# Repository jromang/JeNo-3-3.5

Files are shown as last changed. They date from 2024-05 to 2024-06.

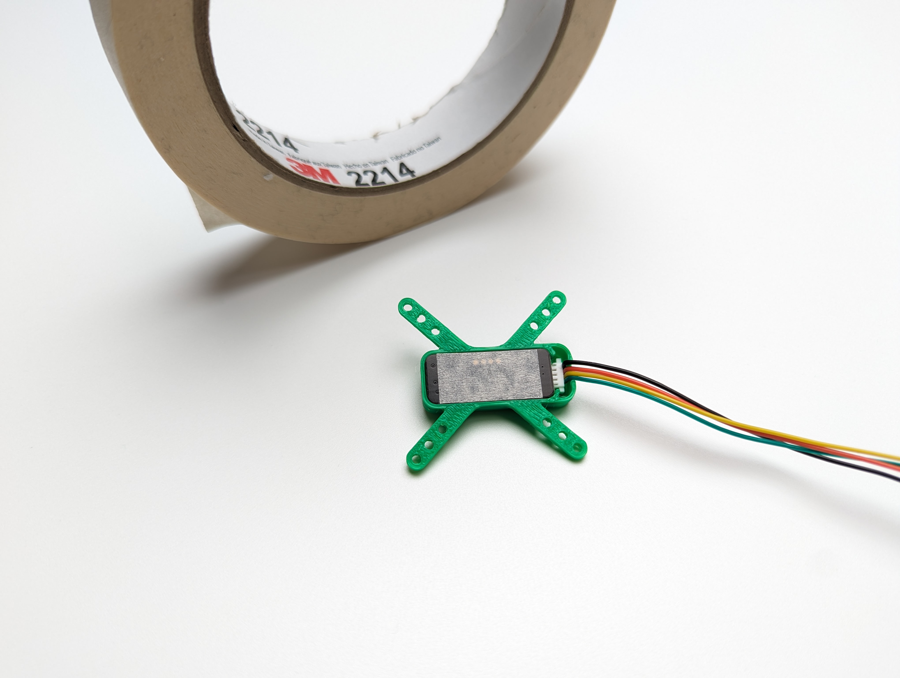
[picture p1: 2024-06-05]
STL/OPTICAL FLOW & LIDAR SENSOR MTF-02 CASE - 6509445/images/1ab90a31-745e-49bc-8f16-971fccf6d18a.jpg

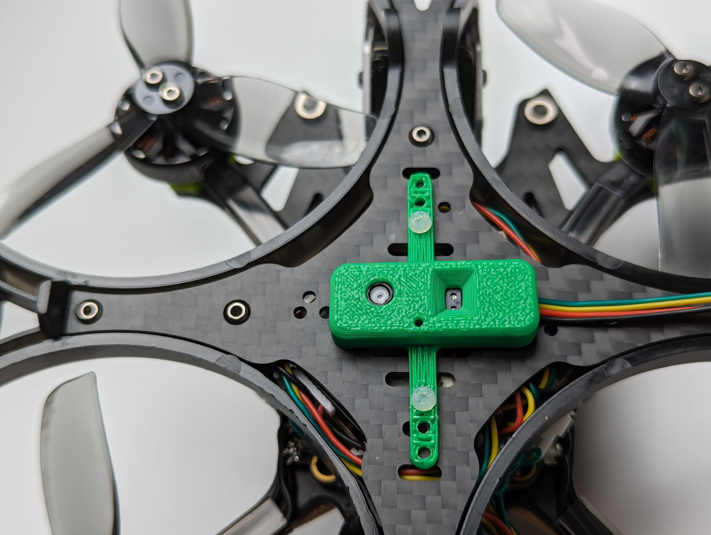
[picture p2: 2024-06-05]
STL/OPTICAL FLOW & LIDAR SENSOR MTF-02 CASE - 6509445/images/625f6806-070a-460f-9479-def415a27e60.jpg

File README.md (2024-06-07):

# Notes de projet JeNo 3

Ce repository contient les notes, liens, et fichiers nécessaires à la construction d'un drone JeNo 3 pouces.

<!-- a normal html comment 

# Liste de courses D

| | Poids unitaire (g) | nombre | Poids total (g) | Prix (€) | Prix unitaire | Remarque |
|-|---|---|---|---|---|---|
|Chassis 3 ‘’ | 56,0 | 1 | 56,0 | 64,50 | 64,50 |
|Stack | 14,4 |1| 14,4 |55,66| 55,66| SpeedyBee F405 Mini 20x20
|Moteur FlyFish | 9,0 |0 |0,0| 62,41
|Moteur Skystars | 8,8| 4 |35,2 |43,84| 43,84 |Skystars Koto 1404 3800KV 3-4S non dispo mais choix ensuite
|Récepteur | 0,7 |1 |0,7 |25,23 |25,23 |FrSky R9 Mini-OTA
|antenne récepteur | 1,5| 1| 1,5
|Gps | 4,3 |1| 4,3| 16,68| 16,68| Walksnail WS-M181
|hélice | 1,50 |4 |6,00| 2,00| 2,00 |HQProp Durable T3x3x3
|Buzzer | 4,00 |1 |4,00 |5,38 |5,38
|Total base | 122,1 |213,29
|Accu 560 mAh | 58,0 |0| 0,0| 19,90| DOGCOM 14,8V 100C 4S
|Accu 450mAh | 53,0 |1| 53,0| 8,63| 8,63| Ovonic 14,8V 80C 4S
|Total base avec accu |175,1 |221,92
|Kit Avatar Moonlight | 38,5 |0 |0,0 |219,90
|camera 4K | 0 |0,0
|antenne FPV | 2,0 |0 |0,0
|total Avatar 4K |0,0
| Kit Avatar HD V2 Dual | 17,6| 1 |17,6 |159,90| 159,90 |en version 32 Go compat Gyroflow
|camera HD V2 | 7,2 |0| 0,0
|antenne HD 2 | 2,0| 2 |4,0
|total Avatar HD V2 | 21,6
|Kit Avatar HD pro dual | 15,4| 0| 0,0 |194,90
|camera HD| 9,5| 0| 0,0
|antenne HD pro| 2,0| 0| 0,0
|total HD pro dual| 0,0
|Total config FPV| 196,7 |381,82

-->

# Liste de courses

| | Poids unitaire (g) | nombre | Poids total (g) | Prix (€) | Prix unitaire | Remarque |
|-|---|---|---|---|---|---|
|Chassis 3 ‘’ | 56,0 | 1 | 56,0 | 53 | 53 | [FVP CNC Drone T700](https://fpvcncdrone.com/product/jeno-3-unibody/)
|Stack | 16.3 |1| 16.3 |69.74| 69.74| [GOKU F722 Pro Mini V2 45A 32Bit 128K 20X20 Stack](https://flywoo.net/products/goku-f722-mini-v2-40a-bls-20x20-stack)
|Moteur  | 8,8| 4 |35,2 |43,84| 43,84 |[ FlyFishRC Flash 1404 4500 KV ](https://www.flyfish-rc.com/products/flash-1404-4500kv-fpv-motor)
|Récepteur | 4 |1 |4 | 15.52 |15.52 | [0.4g Flywoo TCXO 2.4G ELRS EL24E \ EL24P](https://flywoo.net/products/0.4g-flywoo-tcxo-2.4g-elrs-el24e-el24p)
|Gps | 2.2 |1| 2.2 | 17.56| 17.56| [GOKU Nano V3 Flywoo](https://flywoo.net/products/goku-gm10-nano-v3-gps)
|Hélice | 1,50 |4 |6,00| 2,00| 2,00 |HQProp Durable T3x3x3
|Buzzer | 2,7 |1 |2,7 |8.25 |8.25 | [FLYWOO Finder V1.0 w/ LED BUZZER](https://flywoo.net/products/flywoo-finder-v1-0-w-led-buzzer)
|Accu 750mAh | 66,9 |1| 66,9| 15| 15| [Explorer 4S 750mAh HV 80C Lipo Battery - XT30](https://flywoo.net/products/2pcs-explorer-750mah-hv-15-2v-80c-4s1p-lipo-battery-pack-xt30)
|Camera / VTX| 36.4 | 1 | 36.4 | 220 | 249 | [DJI O3 Air Unit](https://www.dji.com/fr/o3-air-unit)
|**Total**|  | | **225,7** | **444.91** |

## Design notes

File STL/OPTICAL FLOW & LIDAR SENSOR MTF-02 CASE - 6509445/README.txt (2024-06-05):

OPTICAL FLOW & LIDAR SENSOR MTF-02 CASE by sr71 on Thingiverse: https://www.thingiverse.com/thing:6509445

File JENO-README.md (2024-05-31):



JeNo 3 - Front view

# JeNo 3" and 3.5"
***3-3.5" drone FPV frame compatible with Air Unit O3 and designed for Freestyle, Freeride and Cinematic. Many customizable options are available.***

> [!NOTE]
> Designed in France by members of the [WE are FPV](https://www.wearefpv.fr/) community, the JeNo is already flown by hundreds of pilots. The French version of the project is available on [Printables](https://www.printables.com/fr/model/459702-jeno-335-drone-frame). Note that a [5.1-6" version](https://github.com/WE-are-FPV/JeNo-5.1) and a [7" version](https://github.com/WE-are-FPV/JeNo-7) of the JeNo exist.

JeNo classic - 3D render

## Table of contents

* [Key features](#key-features)
* [Presentation](#presentation)
* [Detailed specifications](#detailed-specifications)
* [Customization](#customization)
* [Buy it or cut it !](#buy-it-or-cut-it-)
* [Bill of materials](#bill-of-materials)
* [Building/Assembly guide](#buildingassembly-guide)
* [Inspiration](#inspiration)
* [Tuning, Betaflight Preset ?](#tuning-betaflight-preset-)
* [Blackbox](#blackbox)
* [Videos](#videos)
* [Builds examples](#builds-examples)
* [Authors](#authors)
* [TPU](#tpu)
* [Community (remixes and TPU)](#community-remixes-and-tpu)
* [Changelog](#changelog)

## Key features
- [x] **Sturdiness** and **rigidity**
- [x] Excellent flight **performances**, easy to tune
- [x] **Wide-X** geometry
- [x] Perfect DJI **Air Unit O3** camera integration
- [x] Optional soft mounting of the camera for effective Gyroflow stabilization.
- [x] Designed for : DJI Vista/AU O3, WalkSnail, HDZero, Analogic
- [x] **Frame and standoffs NOT visible** in video feed, with any FPV camera
- [x] **Props NOT visible** in video feed !
- [x] Support 20x20 stacks as well as AiO (straight and 45° angled)
- [x] **Customizable** (weight, size, camera plates, unibody or not)

## Presentation
The success of the [JeNo 5.1"](https://github.com/WE-are-FPV/JeNo-5.1) has led us to develop a little brother, in **3 and 3.5"** form factor. This frame will therefore be just **as comfortable for Freestyle as for cinematic** shooting.

On 5" and larger builds, we might be tempted to keep an Action Cam, whereas on a **compact and light machine**, the **DJI O3 reveals its full potential**.

The design of a frame of this size turned out to be more delicate than expected :

* **Weight** is crucial
* **Strength** and **rigidity** remain major concerns
* **Electronics** are more **diversified** : 20x20 stack with separate FC and ESCs, AiO straight or angled at 45°, stack mounting with M2 or M3...
* The low inertia of this format makes the gyro of the O3 camera very sensitive; vibration tolerance is much lower than for a 5" quads
* **Clear FOV** : no spacers, frame, or visible propellers in the FPV feed

After several iterations, we have come to a first version of the JeNo that **ticks all these boxes !** This is the **3" Classic version, unibody with a 4mm bottom plate**.

We were initially not enthusiastic about the unibody design, but this approach has proven to be an **excellent compromise**. With a thickness of 4mm for the bottom plate, we get **exceptional strength** and **flight behavior** worthy of a 5". The assembly remains easy, and the absence of separate arms allows for sliding a 20x20 stack while taking advantage of the 20mm height of the body.

WE are FPV banner

**Other versions** are available :

* 3.5" (unibody) (warning : tips of props slightly visible in the FPV feed)
* 3" (unibody) **Light**
* 3" et 3.5 " with **separate arms**
* 4": this is a variation created by Kennytak, and the necessary files are available on [his page](https://www.printables.com/fr/model/516544-jeno-4-unibody-drone-frame-for-dji03-airunit-vista). The props remain slightly visible in the FPV feed.

The **JeNo 3** follows in the footsteps of its big brother : the front cage tilted at 25° provides a **clear FOV**. Notches are provided to slide in any type of **ND filter**, and the propellers are not visible in the FPV feed or in HD recording.

Two types of camera plates are available : **full carbon** or **soft-mounted**. Note that to benefit from Gyroflow (or RockSteady) stabilization, it is **imperative to opt for the soft-mounted camera plates**.

Finally, as this frame was designed by members of the [WE are FPV](https://www.wearefpv.fr/) **community**, a **"WaF edition"** is available (the logo is engraved on the bottom plate). Join us on the WAF forum in [the official JeNo 3-3.5" thread](https://forum.wearefpv.fr/topic/20437-jeno-335-un-ch%C3%A2ssis-compact-taill%C3%A9-pour-le-dji-o3/) to discuss it further.

WE are FPV banner

The JeNo is also available in [5.1-6" version](https://github.com/WE-are-FPV/JeNo-5.1) and [7" version](https://github.com/WE-are-FPV/JeNo-7).

## Detailed specifications

||| 
| :--- | :--- |
| **Geometry** | **Wide-X** | 
| **Props size** | 3 to 3.5" (depending on the versions) | 
| **Weight** | **40 to 55 g** depending on the versions, including screws | 
| **Arms** | **4mm** for unibody, **3mm** for separate arms | 
| **Body height** | 20 mm | 
| **Stack height** | 20 mm (unibody) | 
| **Bottom plate** | **4mm** for unibody, **2mm** for separate arms | 
| **Middle plate** | 2 mm (separate arms) | 
| **Top plate** | 2 mm | 
| **Camera plates** | 2.5 mm | 
| **Motors mounting** | 9 to 12 mm | 
| **Camera** | 20 mm (DJI), Micro, Nano. **Clear FOV**. Ajustable.
| **Main stack** | 25.5 mm x 25.5 mm (M2) AiO and 20 mm x 20 mm (M2) stack | 
| **Supported VTX** | Analogic, DJI Vista, **DJI Air Unit O3**, WalkSnail, HDZero… | 
| **Strap passage** | Yes | 

## Customization

The JeNo is customizable, offering several **options** to best adapt to different needs and individual preferences : 

* **3" Unibody 4mm Classic :** This is the first version made available. Designed for **freestyle** due to its strength, it will also be suitable for **cinematic** use with soft-mounted camera plates. 100% clear FOV. This version uses **M3** screws and standoffs.
* **3" Unibody 4mm Light :** Sacrificing some strength and rigidity for more lightweight, thus increasing autonomy, and switching to **M2** screws/spacers. A chassis more oriented towards cinematic use. Note that M2 standoffs are more difficult to source.
* **3.5" Unibody 4mm :** For those seeking a bit more **inertia and stability**, or possibly for mid-range use. _**Note: the propellers are very slightly visible in the FPV feed. With black propellers, they will be practically invisible.**_
* **Separate arms :** For those wary of unibody designs ;) a 3" version and a 3.5" version (only the length of the arms changes). _**Note: AIO strongly recommended; stacks will struggle to fit due to the low remaining height in the body = low profile !**_

Two versions of 25° **camera plates** are available: **freestyle** (full carbon) or **cinematic** (soft-mounted). 

> [!IMPORTANT]
> Please note that to benefit from Gyroflow (or RockSteady) stabilization, **soft mounting is mandatory**.

A [high tilt version](https://www.thingiverse.com/thing:6584519) (40°) is available in community remixes (by [Bard Fpv](https://www.youtube.com/@bardfpv)).

> [!IMPORTANT]
By default, we have left the stack holes at a 2mm diameter (M2). If your stack uses M3 screws, you will need to enlarge these holes. Please note, carbon dust is hazardous, to avoid inhaling it, run a trickle of water while drilling/filing.

For your information, we have tested this frame with the following setup:

* **Recommended Motors :** 1404, 4000 to 4500KV for 3"
* **Recommended Batteries :** 4S / 550mAh for Freestyle, up to 850mAh for cinematic cruising
* **Recommended Props :** T3x2.5x3 & HQ T3x3x3

Below, you will find a complete build example as well as several flight videos with this setup.

## Buy it or cut it !

Like the 5.1" version, the JeNo 3" should be available from [Drone FPV Racer](https://www.drone-fpv-racer.com/) in a near future.

The ["dxf"](https://github.com/WE-are-FPV/JeNo-3-3.5/tree/main/dxf) folder contains all the files you need to get it **cut** in your favourite flavour :

* **JeNo_3inch_M3.dxf :** Classic 3" 4mm unibody frame
* **JeNo_3inch_Unibody_light_M2.dxf :** Light 3" 4mm unibody frame
* **JeNo_3.5inch_M3.dxf :** Classic 3.5" 4mm unibody frame
* **JeNo_3inch_multiplates_M3.dxf :** Separate arms 3" frame
* **JeNo_35inch_multiplates_M3.dxf :** Separate arms 3.5" frame 

> [!NOTE]
> Each file contains all parts.
> All camera plates versions are included in the files.

["extras"](https://github.com/WE-are-FPV/JeNo-3-3.5/tree/main/dxf/extras) folder will contain specific and optional parts.

## Bill of materials

In addition to the carbon fiber, you will need the following hardware to complete the assembly of the frame.

**Standoffs**

It is recommended to use 5mm diameter standoffs, especially for those that will serve as support for TPU (backpack and capacitor). Moletted standoffs can still be used, but the TPU supports will need to be modified accordingly.

> [!WARNING]
> Attention: For the Light version, you will need to provide M2 standoffs and corresponding screws (M2 instead of M3)

| Quantity | Description | Details |
| :---: | :--- | :--- |
| 6 | M3x20mm standoffs | for the body |
| 2 | M3x20mm standoffs | for the camera |

**Stack materials**

> [!WARNING]
> Attention: M2 screws are mentioned here because they are most commonly found in this format. However, some 20x20 stacks use M3 screws. In this case, you will need to enlarge the stack holes.

* If 25.5x25.5 AiO

| Quantity | Description | Details |
| :---: | :--- | :--- |
| 4 | M2x16mm | for the stack |
| 4 | M2 nuts for stack screws | |

* If 20x20 stack

| Quantity | Description | Details |
| :---: | :--- | :--- |
| 4 | M2x20mm countersunk screws | for the stack |
| 4 | M2 nuts for stack screws | |

**Frame materials**

| Quantity | Description | Details |
| :---: | :--- | :--- |
| 6 | M3x6/8mm countersunk screws | for the top plate |
| 10 | M3x8mm screws (titanium if possible) | for the bottom and camera plates |

**Additional materials**

| Quantity | Description | Details |
| :---: | :--- | :--- |
| 16 | M2x7mm screws (if using arms protections) or M2x6mm (if no TPU) | for the motors |
| 4 | M2x3mm screws if soft mounted or M2x4mm if NOT softmounted | for the camera |

**Additional materials for separate arms versions**

| Quantity | Description | Details |
| :---: | :--- | :--- |
| 5 | Pressnuts ([Flywoo](https://www.drone-fpv-racer.com/flywoo-m3-clinch-nuts-20-pcs-7965.html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) or SourceOne alike) | 4 for the arms, 1 for the middle plate |
| 5 | M3x10mm screws | for the pressnuts |

**Fasten the lipos**

The JeNo allows the use of non-slip straps thanks to its strap slots. You can also use a LiPo pad if desired.

## Building/Assembly guide
Some **clarifications** before assembling the frame:

* If your electronics require M3 screws, you will need to slightly enlarge the holes, originally designed for M2 (taking care not to inhale carbon dust)
* You can use the front standoffs to attach a capacitor and/or an RX :

JeNo 3 Capacitor and RX

* The RX antenna can be attached to the front of the quad using zip ties (TPU front bumper also allow to fix the RX antenna)

JeNo 3 RX Antenna

The assembly is simple (you can also find the detailed [assembly instructions in PDF format](https://github.com/WE-are-FPV/JeNo-3-3.5/blob/main/docs/Assembly_Guide_JeNo3_en.pdf) among the project files) :

JeNo 3 Assembly step 01

JeNo 3 Assembly step 02

JeNo 3 Assembly step 03

JeNo 3 Assembly step 04

JeNo 3 Assembly step 05

## Inspiration
It is primarily inspired by its big brother, the [JeNo 5.1"](https://github.com/WE-are-FPV/JeNo-5.1), especially for the camera plates system.

## Tuning, Betaflight Preset ?
For the JeNo 5.1", we provided a preset.

For the 3", we will not share a preset in the short term because there are **too many factors** that can alter the quad's behavior:

* Bottom plate thickness
* Stack VS AiO (the latter often being much noisier)
* M3 screws and spacers vs M2
* 3" props vs 3.5"
* Capacitor or not
* etc.

If, with a little more perspective, we see that a preset is feasible, we will share it. In the meantime, we have shared some settings that should work with most setups in [this post](https://forum.wearefpv.fr/topic/20437-jeno-335-un-ch%C3%A2ssis-compact-taill%C3%A9-pour-le-dji-o3/page/10/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).

However, one piece of advice, if you find your quad too challenging to handle in confined spaces, do not hesitate to adjust the throttle curve by adding a bit of expo around the "hover point" :

JeNo 3 Throttle curve

## Blackbox
Here is an overview of vibration distribution on the 3 axes for the JeNo 3" 4mm Unibody. This is indeed the **unfiltered** gyro signal freestyle flight :

JeNo 3 Blackbox

## Videos
Flight preview of the JeNo 3" Unibody Classic 4mm version (Cinematic, camera plates soft-mounted), stabilized with Gyroflow :

JeNo 3" Cinematic (https://www.youtube.com/watch?v=Bba9C5jj3qI "JeNo 3 Cinematic - Click to Watch!")

Flight preview of the JeNo 3" Unibody Classic 4mm version (Freestyle) :

JeNo 3" Freestyle (https://www.youtube.com/watch?v=a-RcqAQSSa8 "JeNo 3 Freestyle - Click to Watch!")

Flight preview of the JeNo 3" Unibody Classic 4mm version (Bando):

JeNo 3" Bando (https://www.youtube.com/watch?v=Iw_Cw9_1gNU "JeNo 3 Bando - Click to Watch!")

JeNo 3" review on WE are FPV (French) :

JeNo 3" Review (https://www.youtube.com/watch?v=-c4rGYWvYhU "JeNo 3 Review - Click to Watch!")

## Builds examples
You can find many build examples on [WE are FPV's DroneBuilds](https://forum.wearefpv.fr/71-dronebuilds/) :

* fr : [JeNo 3 Prototype](https://forum.wearefpv.fr/topic/20327-proto-jeno-3/) (this one)
* fr : [JeNo 3" AiO AT32/AM32](https://forum.wearefpv.fr/topic/21637-jeno-3-aio-at32am32/)
* fr : [JeNo 3.5" O3](https://forum.wearefpv.fr/topic/20480-jeno-35_o3/)
* fr : [JeNo 3" (6s)](https://forum.wearefpv.fr/topic/22032-jeno-3-mais-en-6s-et-sous-testost%C3%A9rone/)
* fr : [Jeno 3" (Kiss)](https://forum.wearefpv.fr/topic/21647-jeno-3-kiss/)
* fr : [jeno3 light](https://forum.wearefpv.fr/topic/22677-jeno3-light/)
* ...

## Authors

The JeNo was designed by :

* nochamo - [Youtube](https://www.youtube.com/user/nochamo)
* Jerome / Jéjé FPV - [Youtube](https://www.youtube.com/@jejefpv)

## TPU
Among the [downloadable files](https://github.com/WE-are-FPV/JeNo-3-3.5/tree/main/tpu), you will find a variety of TPU to protect your JeNo 3" :

* **VTX Antenna** mounts
* Front and back **bumpers**
* **Nano camera** adapter
* Camera **softmount**
* Several arms **protections**

## Community (remixes and TPU)

**Fork/remix**

* [JeNo 4"](https://www.printables.com/fr/model/516544-jeno-4-freestyleracing-drone-frame-for-dji03-airun) by [Kennytak](https://www.printables.com/fr/@Kennytak_77000)

**TPU**

In addition to the TPU options available on [this repo](https://github.com/WE-are-FPV/JeNo-3-3.5/tree/main/tpu), you will find here some TPU designs created by the community.

* [TPU set for JeNo 3.5"](https://www.printables.com/fr/model/533320-tpu-pour-jeno-35) by Xavier Robin
* [GPS and O3 antenna mounts](https://www.printables.com/fr/model/595138-jeno-3-antenne-option-gps-18x18x8) by Olivier
* [Shark fin to protect the lipo](https://www.thingiverse.com/thing:6416888) by vfr150878
* [Backpack O3 antenna + GPS M10 mini](https://www.printables.com/fr/model/794568-jeno-3) by [Cirbaf](https://www.printables.com/fr/@Cirbaf_1779503)
* [Arms/motors bando protections](https://www.printables.com/fr/model/649175-bando-boots-jeno-3p) by Julien
* [Runcam Thumb mount](https://www.printables.com/fr/model/647336-mount-runcam-thumb-pour-jeno3)by [Tamm'c](https://www.printables.com/fr/@TammC_1383304)
* [TPU set + 40° high tilt camera plates](https://www.thingiverse.com/thing:6584519) by [Bard Fpv](https://www.youtube.com/@bardfpv)
* [Front bumper](https://www.printables.com/fr/model/876097-bumper-jeno-3) by [Nox](https://www.printables.com/fr/@NOX_1685274)
* [M10 Mini Support, Cap, ViFly Finder, O3 Antenna](https://www.printables.com/fr/@NnJj_1076330/models) by [Nn Jj](https://www.printables.com/fr/@NnJj_1076330)

## Changelog

> [!TIP]
> Compatibility is consistently maintained between each version: if your frame was a v1, the parts from v1.2 will be compatible. The same applies to TPU accessories. That's why we don't keep the history of previous versions.

* **28/04/2023 :** Version 1.0

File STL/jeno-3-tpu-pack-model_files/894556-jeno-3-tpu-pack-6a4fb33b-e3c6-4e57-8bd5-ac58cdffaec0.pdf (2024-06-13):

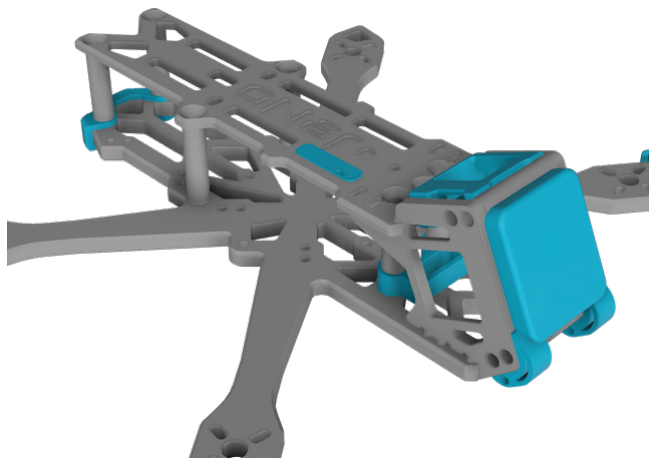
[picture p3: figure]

1.04 hrs

4 pcs

f

0.20 mm

k

0.40 mm

h

Flex

8 g

d

Prusa
MK3/S/S+

## Summary

Pack of TPUs for the JeNo 3 FPV model designed by WAF.

Hobby & Makers (https://printables.com/model?categoryId=48) > RC & Robotics (https://printables.com/model?categoryId=64)

Tags: | tpu | jeno3

This pack modify/add 4 TPUs parts on the great JeNo 3 designed by WAF :

a tiny landing pad design
a GPS nano M10Q support above O3 camera
an ELRS BetaFPV Nano RX support behind the O3 camera, hold by the Spacers.
a compact bumper back
a bumper front splitted in 2 pieces (Left & Right) with ELRS antenna holes
a blocker for ziptie holding the LIPO battery cable on the top plate

Printed in Sain Smart TPU in 15% Infill, 0.2mm layer height without brim.

N (https://printables.com/@Nono31_454985) Nono31 (https://printables.com/@Nono31_454985)

## JeNo 3 TPU pack

VIEW IN BROWSER (https://printables.com/model/894556-jeno-3-tpu-pack)

updated 5. 6. 2024 | published 5. 6. 2024

•
•
•

•
•

•

## Model files

Some part needs to activate support with Organic style (see Gcode)

## This remix is based on

JeNo 3"/3.5" Drone Frame (https://printables.com/model/459702-jeno-335-drone-frame)
by WE are FPV (https://printables.com/@WEareFPV_476425)

jeno3_gps_nano.stl

jeno3_arm_pad.stl

jeno3_bumper_back.stl

jeno3_support_elrs.stl

bumper-front-left.stl

attach-lipo-cable.stl

## Print files

h Flex k 0.40 mm f 0.20 mm 0.31 hrs 1 g d Prusa MK3/S/S+

h Flex k 0.40 mm f 0.20 mm 0.48 hrs 3 g d Prusa MK3/S/S+

h Flex k 0.40 mm f 0.20 mm 0.17 hrs 1 g d Prusa MK3/S/S+

h Flex k 0.40 mm f 0.20 mm 0.08 hrs 1 g d Prusa MK3/S/S+

## License

This work is licensed under a
Creative Commons (4.0 International License)

Attribution-NonCommercial (http://creativecommons.org/licenses/by-nc/4.0/)

✖ | Sharing without ATTRIBUTION
✔ | Remix Culture allowed
✖ | Commercial Use
✖ | Free Cultural Works
✖ | Meets Open Definition

jeno3_gps_nano_02mm_flex_mk3s_19m.gcode

jeno3_arm_pad_02mm_flex_mk3s_29m.gcode

jeno3_bumper_back_02mm_flex_mk3s_10m.gcode

jeno3_support_elrs_02mm_flex_mk3s_5m.gcode

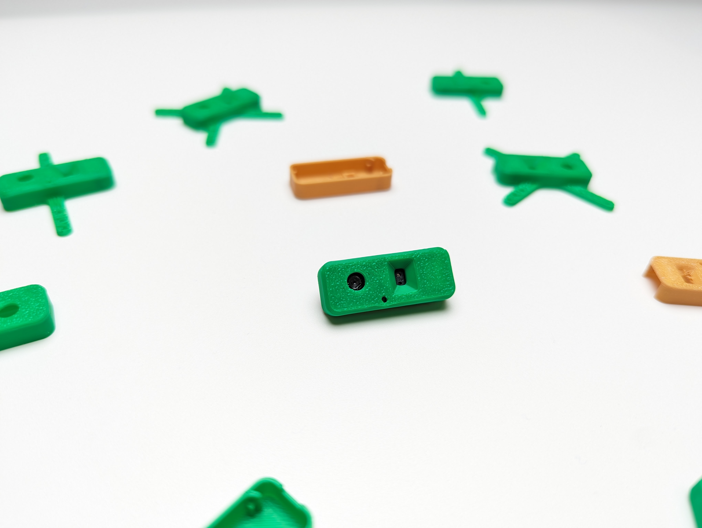
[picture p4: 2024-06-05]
STL/OPTICAL FLOW & LIDAR SENSOR MTF-02 CASE - 6509445/images/302a0b4c-784a-471d-8746-ba2570d10bce.jpg

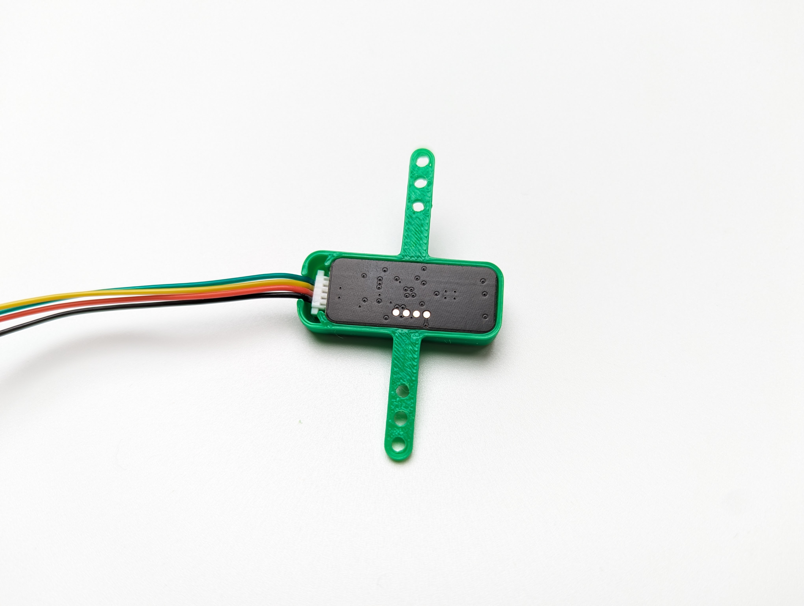
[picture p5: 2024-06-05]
STL/OPTICAL FLOW & LIDAR SENSOR MTF-02 CASE - 6509445/images/a6944667-2f63-432b-88a1-bd5ccdd9be9f.jpg

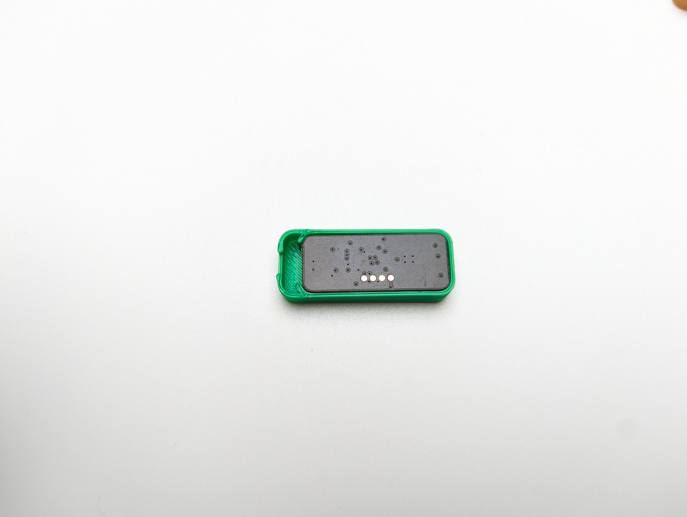
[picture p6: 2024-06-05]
STL/OPTICAL FLOW & LIDAR SENSOR MTF-02 CASE - 6509445/images/054b09f2-f21a-4c70-822b-3b0b492575ab.jpg

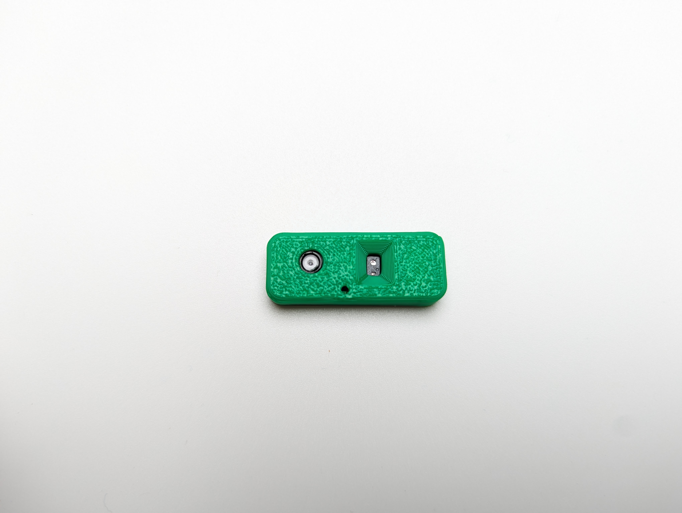
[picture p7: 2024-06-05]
STL/OPTICAL FLOW & LIDAR SENSOR MTF-02 CASE - 6509445/images/14cd47e6-1254-4f28-a62e-50993b2ca222.jpg

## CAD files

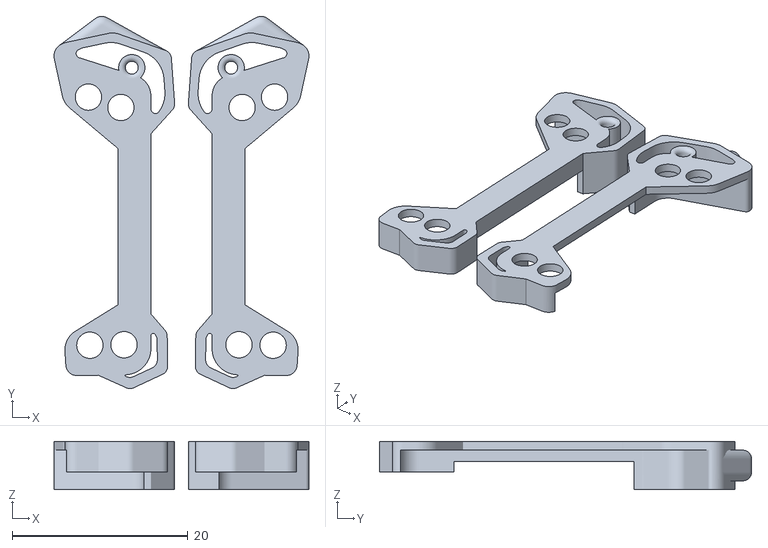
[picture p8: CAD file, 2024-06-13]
STL/bumper-jeno-3-model_files/bumper haut v2.stl.stl
29.0 x 42.4 x 5.50

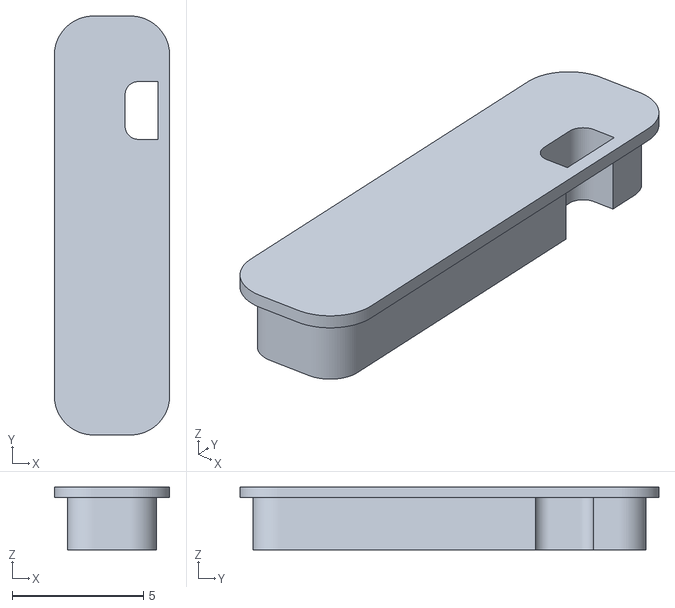
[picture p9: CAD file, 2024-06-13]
STL/jeno-3-tpu-pack-model_files/attach-lipo-cable.stl
4.40 x 16.0 x 2.40

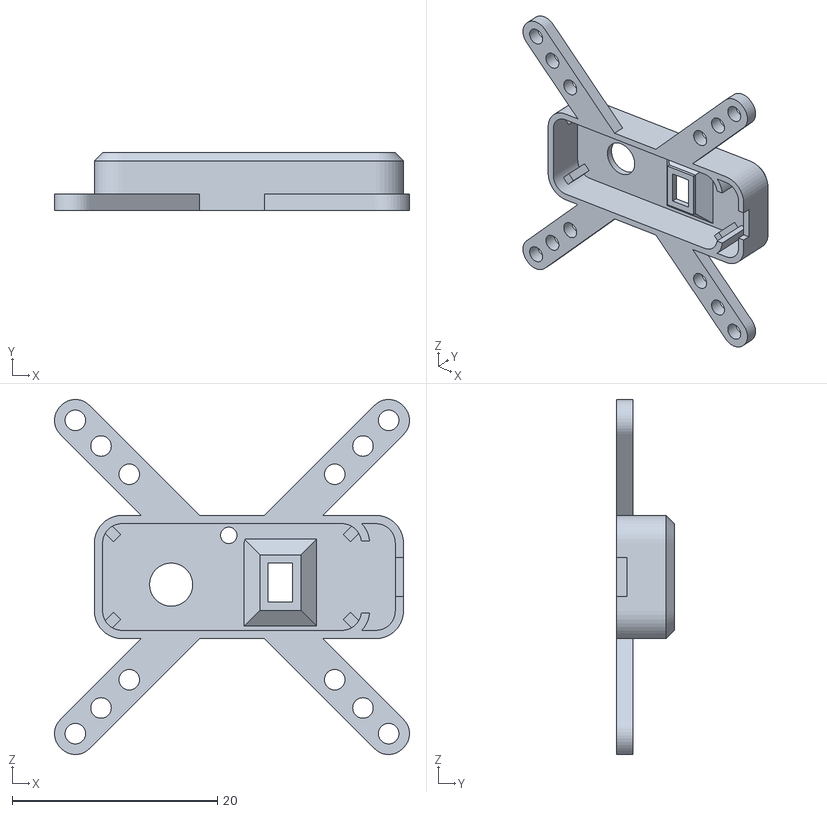
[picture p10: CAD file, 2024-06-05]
STL/OPTICAL FLOW & LIDAR SENSOR MTF-02 CASE - 6509445/files/Mico_Air_MTF-02_OPTICAL_FLOW__LIDAR_SENSOR_case3.STL
34.6 x 5.60 x 34.6

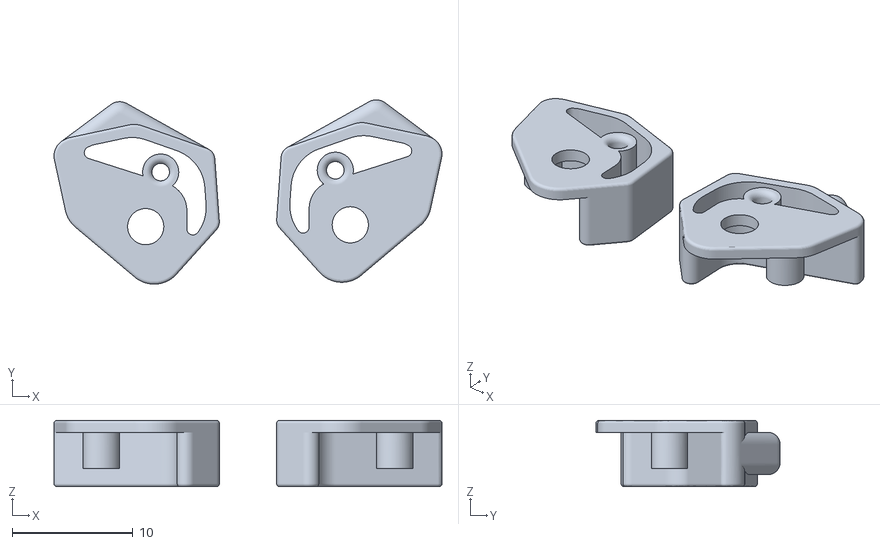
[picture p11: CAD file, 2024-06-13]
STL/bumper-jeno-3-model_files/bumper jeno 3 ant.stl.stl
32.2 x 15.3 x 5.50

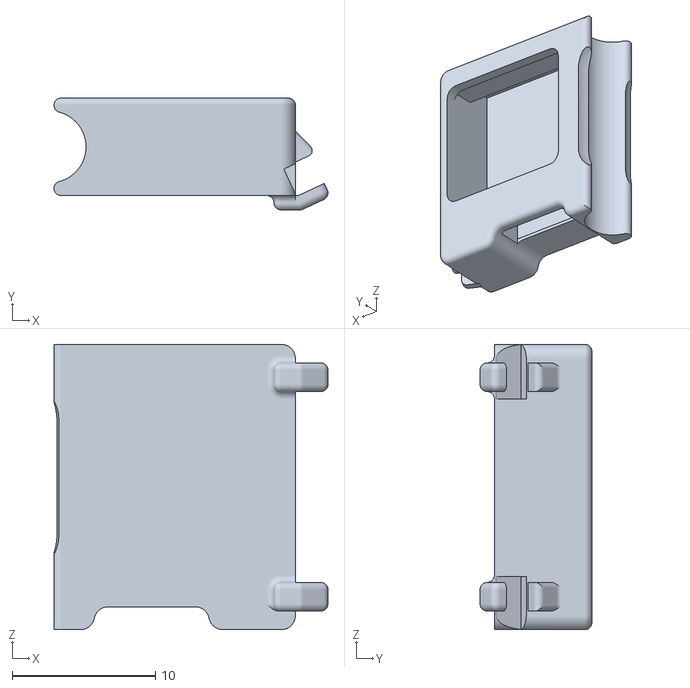
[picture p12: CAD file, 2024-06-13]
STL/jeno-3-tpu-pack-model_files/jeno3_gps_nano.stl
19.1 x 7.80 x 19.9

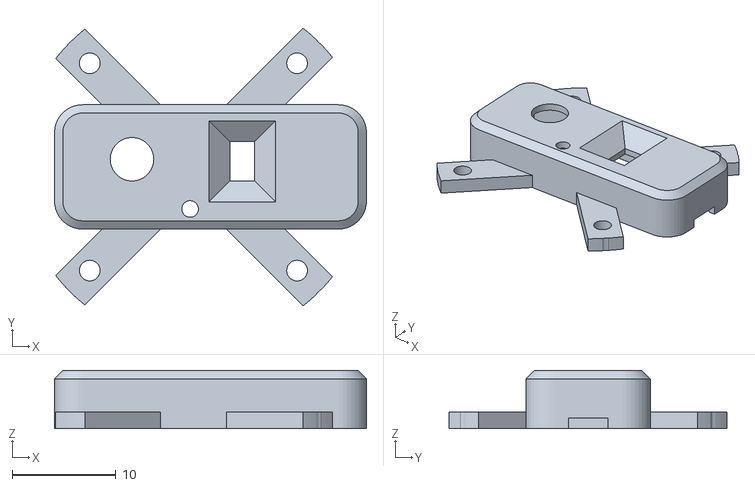
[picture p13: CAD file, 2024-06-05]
STL/OPTICAL FLOW & LIDAR SENSOR MTF-02 CASE - 6509445/files/lidar_X_cut.stl
30.1 x 26.8 x 5.60

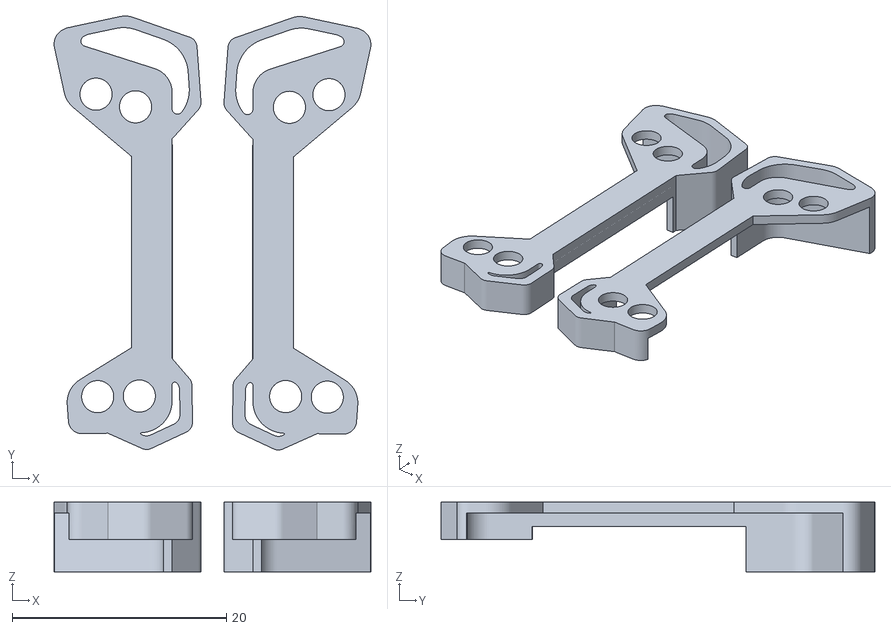
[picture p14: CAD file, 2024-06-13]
STL/bumper-jeno-3-model_files/bumper jeno3v1.stl.stl
29.6 x 40.5 x 6.50

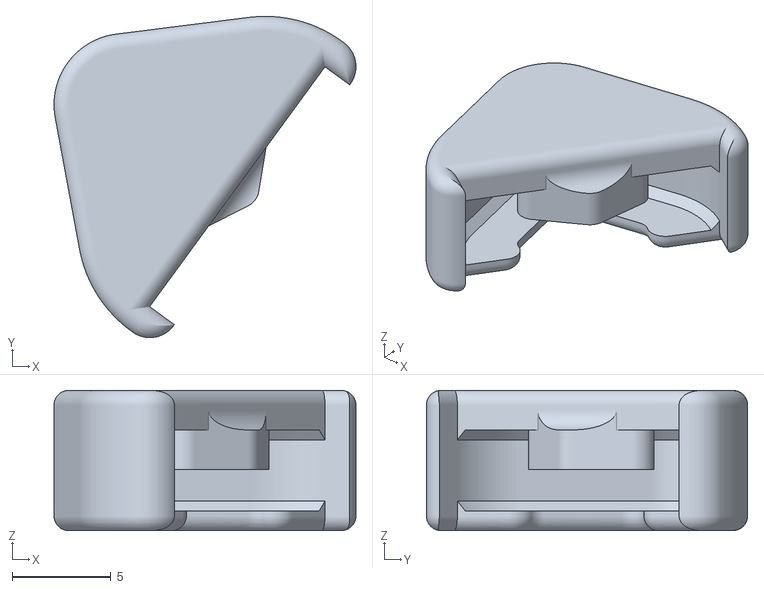
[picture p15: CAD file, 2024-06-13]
STL/jeno-3-tpu-pack-model_files/jeno3_arm_pad.stl
15.3 x 16.3 x 7.10

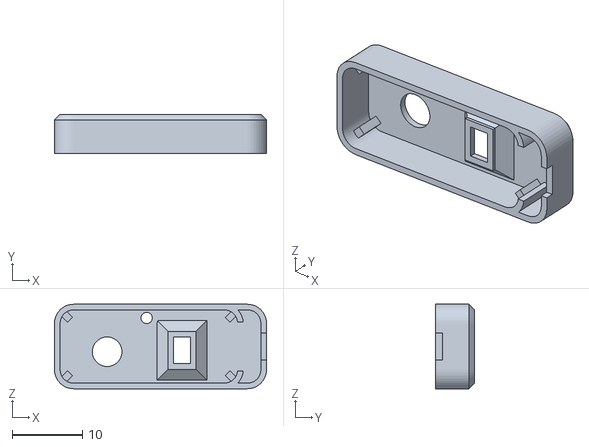
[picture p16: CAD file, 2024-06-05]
STL/OPTICAL FLOW & LIDAR SENSOR MTF-02 CASE - 6509445/files/Mico_Air_MTF-02_OPTICAL_FLOW__LIDAR_SENSOR_case1.STL
30.1 x 5.60 x 12.0

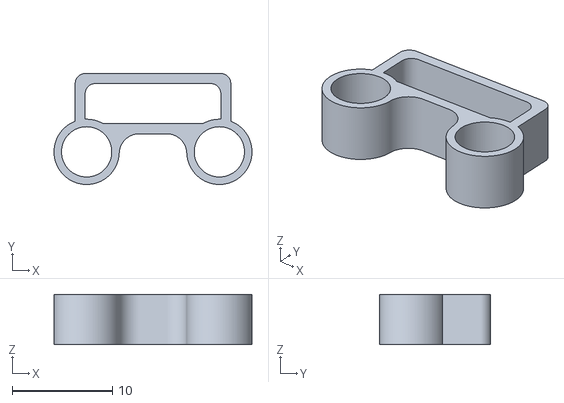
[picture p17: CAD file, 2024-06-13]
STL/jeno-3-tpu-pack-model_files/jeno3_support_elrs.stl
19.7 x 11.0 x 5.00

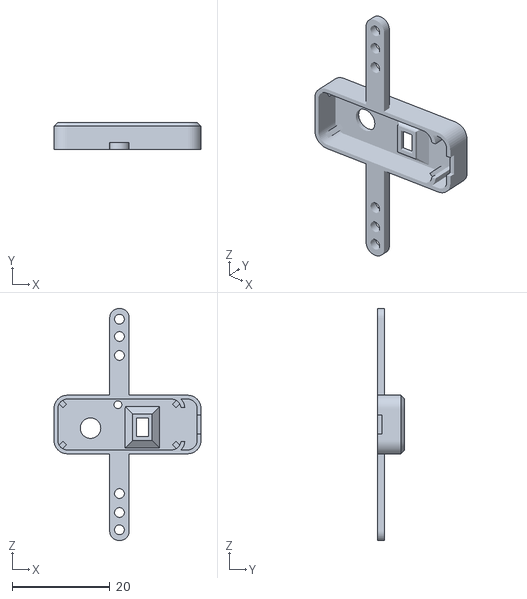
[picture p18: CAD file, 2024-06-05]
STL/OPTICAL FLOW & LIDAR SENSOR MTF-02 CASE - 6509445/files/Mico_Air_MTF-02_OPTICAL_FLOW__LIDAR_SENSOR_case2.STL
30.1 x 5.60 x 47.5

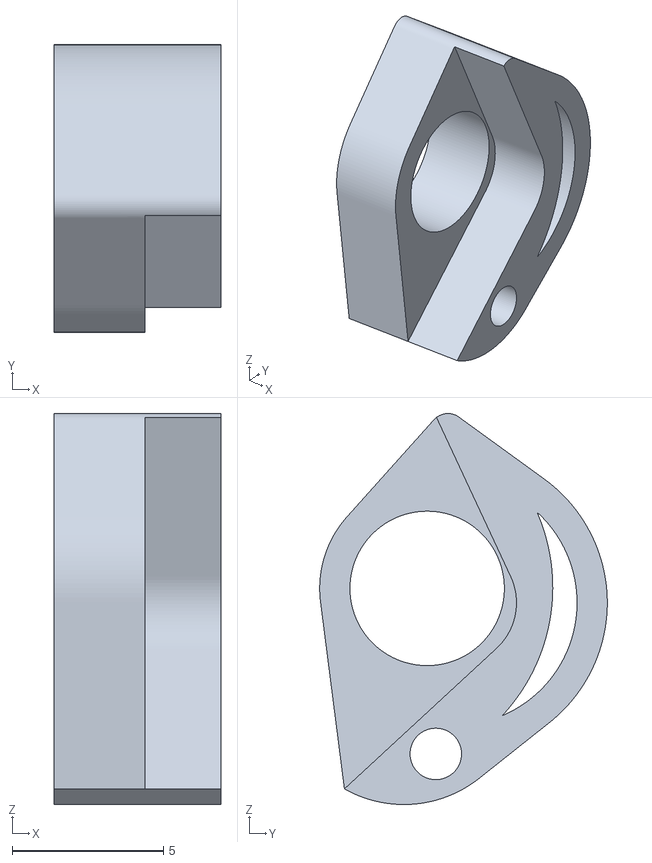
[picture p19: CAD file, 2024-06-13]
STL/jeno-3-tpu-pack-model_files/bumper-front-left.stl
5.50 x 9.50 x 12.9

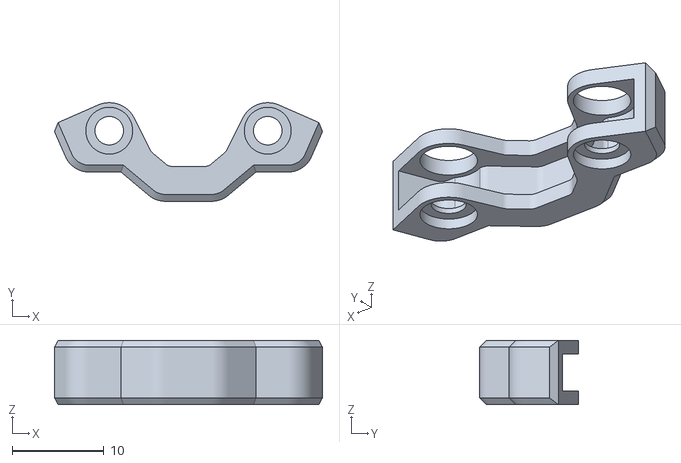
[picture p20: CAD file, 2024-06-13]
STL/jeno-3-tpu-pack-model_files/jeno3_bumper_back.stl
29.2 x 10.7 x 7.00

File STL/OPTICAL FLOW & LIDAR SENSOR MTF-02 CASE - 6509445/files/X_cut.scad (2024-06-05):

intersection(){
cylinder(h=20, r=17.0, center=true, $fn = 200);

translate([-17.4,17.3,0])
rotate([90,0,0])
import("Mico_Air_MTF-02_OPTICAL_FLOW__LIDAR_SENSOR_case3.stl", convexity=3, center=true);
}

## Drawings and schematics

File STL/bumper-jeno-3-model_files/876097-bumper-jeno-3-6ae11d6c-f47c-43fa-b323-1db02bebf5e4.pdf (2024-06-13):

## bumper jeno 3

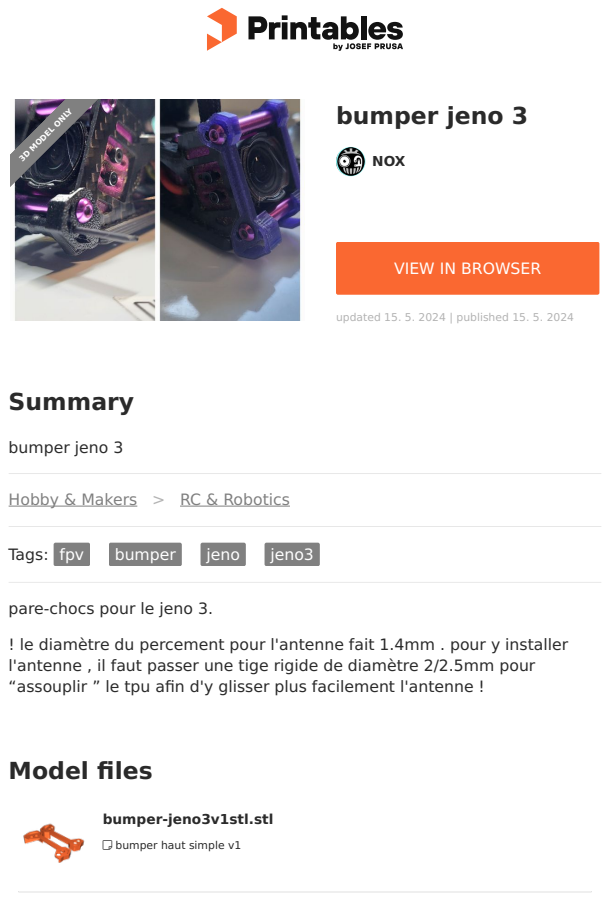
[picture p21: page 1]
Model files; Summary; bumper jeno 3; Tags: fpv; bumper; jeno; jeno3; NOX; updated 15. 5. 2024 | published 15. 5. 2024; bumper-jeno3v1stl.stl; 3D MODEL ONLY

VIEW IN BROWSER (https://printables.com/model/876097-bumper-jeno-3)

Hobby & Makers (https://printables.com/model?categoryId=48) > RC & Robotics (https://printables.com/model?categoryId=64)

pare-chocs pour le jeno 3.

! le diamètre du percement pour l'antenne fait 1.4mm . pour y installer
l'antenne , il faut passer une tige rigide de diamètre 2/2.5mm pour
“assouplir ” le tpu afin d'y glisser plus facilement l'antenne !

bumper haut simple v1

- bumper simple + support antenne
- bumper haut + support antenne

## License

This work is licensed under a
Creative Commons (4.0 International License)

Attribution (http://creativecommons.org/licenses/by/4.0/)

✖ | Sharing without ATTRIBUTION
✔ | Remix Culture allowed
✔ | Commercial Use
✔ | Free Cultural Works
✔ | Meets Open Definition

bumper-jeno-3-antstl.stl

bumper-haut-v2stl.stl

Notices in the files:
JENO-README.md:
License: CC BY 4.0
